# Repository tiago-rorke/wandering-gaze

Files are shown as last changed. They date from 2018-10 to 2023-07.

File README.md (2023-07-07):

# Wandering Gaze

Interactive installation by Ana Teresa Vicente.  
https://anateresavicente.com/wandering-gaze  

The system comprises:
 - core X-Y 2 axisgantry housed in a slightly oversized picture frame
 - a special viewfinder
 	- IR reflectance sensor to detect the person looking through the viewfinder
 	- IR illumination behind a diffusor in the right eye-cup
 	- 45 degree pane of glass reflects the eye into a ps3eye webcam
 	- small LED attached to the side of the webcam lens
 - a tripod containing a mini pc

This installation was largely made possible thanks to the wonderful [EyeWriter](http://eyewriter.org/) project!  We faced a considerable challenge however, in getting (very roughly) accurate tracking from random people approaching the viewfinder without putting them through the calibration process.  We reached a compromise by creating a kind of auto-calibration where a small red dot would appear in the viewers vision when they approach the viewfinder.  They are told to stare at the dot until it disappears, before proceeding to look at the image.  This position is then used to apply an offset to the resulting tracking data to roughly correct it relative to the position of the viewers eye.

## Sources

The eye-tracking sofware is built using the EyeWriter tool and openFrameworks.  
http://eyewriter.org/

CAD model of installation made with Onshape:  
https://cad.onshape.com/documents/b327fc03410528552058d868/w/0ee9eb11091f6ccb3df238ed/e/d6edd997d3fa7512d0595dc8  
the X-Y gantry is based on a previous plotter design:  
https://cad.onshape.com/documents/9c853be8b394a81c5aa6c314/w/0828b5069770ad60c812175c/e/8f06230b793865605afa23f3  
the motion uses the coreXY design:  
http://corexy.org/  
and the structure uses openbuilds:  
https://openbuilds.com/  

The X-Y motion control is done with GRBL  
https://github.com/gnea/grbl  

Arduino is used in the viewfinder and the plotter:  
https://www.arduino.cc/

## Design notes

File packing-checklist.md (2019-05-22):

# Packing Checklist

- Tripod 
    - base
    - 3 metal legs
    - shelf 
    - viewfinder + calibration frame
- Photo frame machine
    - black frame cover 
    - slotted standards
- 1 Ikea stool 
- Screws box 
    - screws
    - power supply + cable
    - viewfinder glass
- Metal shavings box and instructions label
- Debugging box
    ◦ double adapter eu plug
    ◦ router
    ◦ 12v ac-dc adapter + cable
    ◦ 5v ac-dc adapter
    ◦ 2x network patch cables
    ◦ 2x USB micro cables
    ◦ 1x USB mini cable
- Envelope
    - installation assembly and usage overview
    - stool assembly instructions
    - contacts

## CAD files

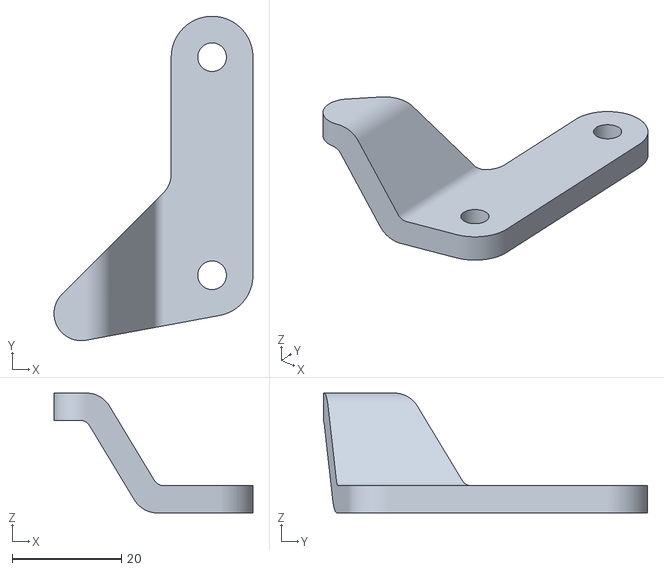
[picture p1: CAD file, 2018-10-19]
design_files/3d_printing/plotter/endstop_batent_v3.stl
36.5 x 59.5 x 22.0

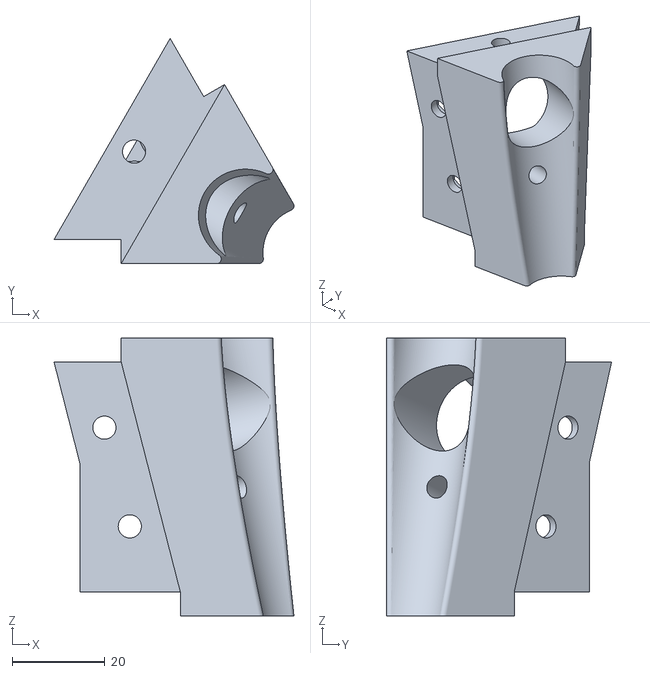
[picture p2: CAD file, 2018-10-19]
design_files/3d_printing/tripe/tripé - corner_right.stl
51.8 x 48.6 x 60.0

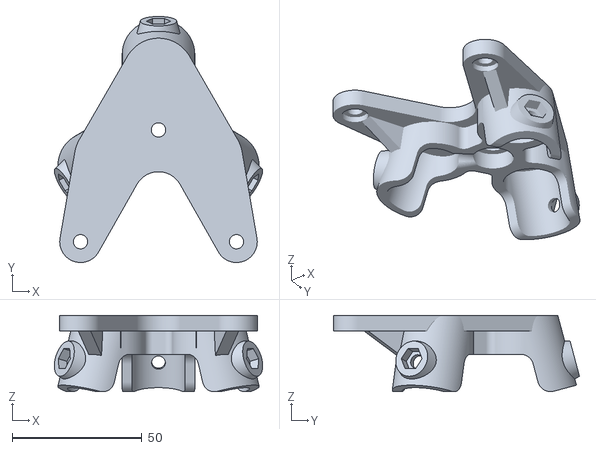
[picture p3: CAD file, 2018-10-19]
design_files/3d_printing/viewfinder/viewfinder v2 - tripod_mount.stl
80.1 x 94.6 x 29.4

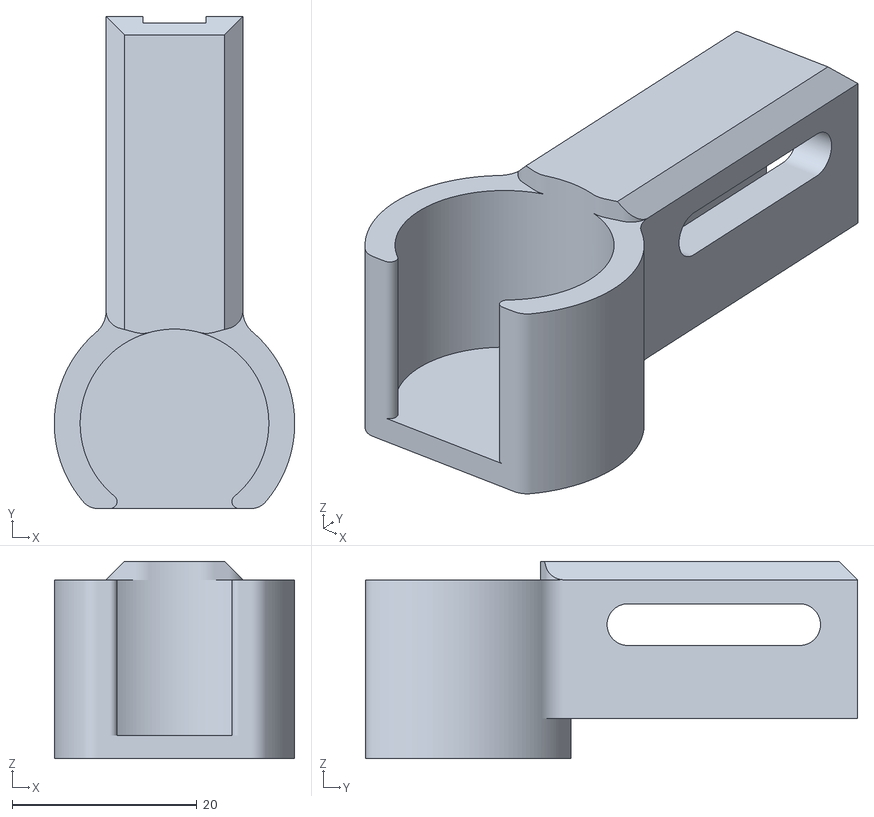
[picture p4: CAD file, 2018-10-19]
design_files/3d_printing/plotter/magnet-holder-20mm_v1.stl
26.0 x 53.2 x 21.4

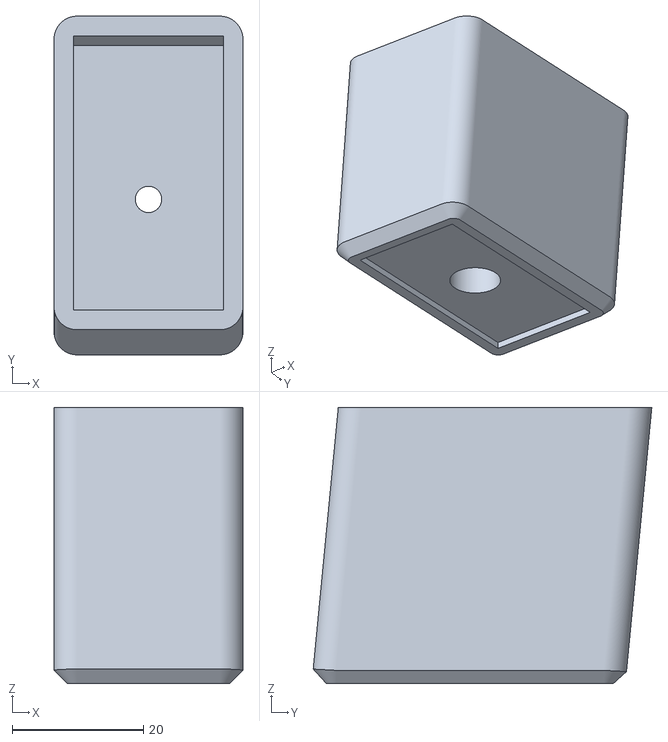
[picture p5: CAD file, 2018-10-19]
design_files/3d_printing/tripe/banco_feet - tall_v2.stl
28.8 x 51.5 x 42.0

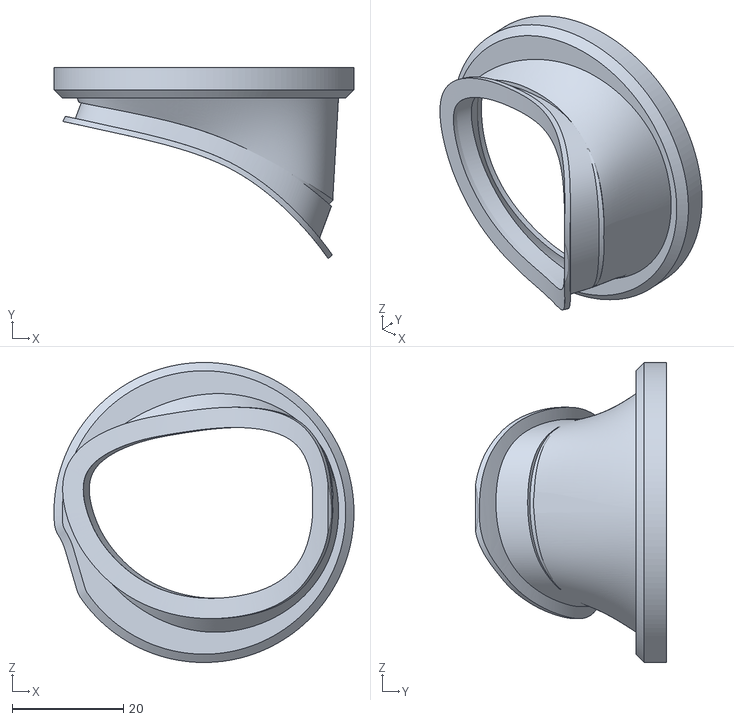
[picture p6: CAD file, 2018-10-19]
design_files/3d_printing/viewfinder/viewfinder v2 - eyecup_right.stl
54.0 x 34.4 x 54.0

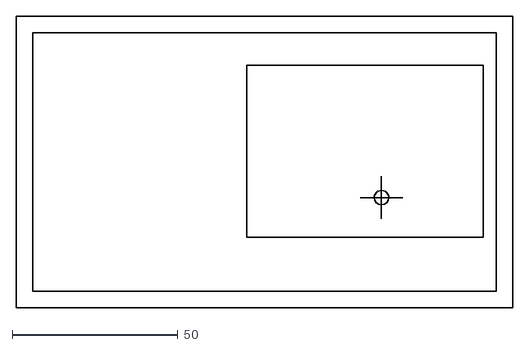
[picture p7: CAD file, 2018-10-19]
design_files/laser_cutting/overlay.dxf
150.0 x 88.0

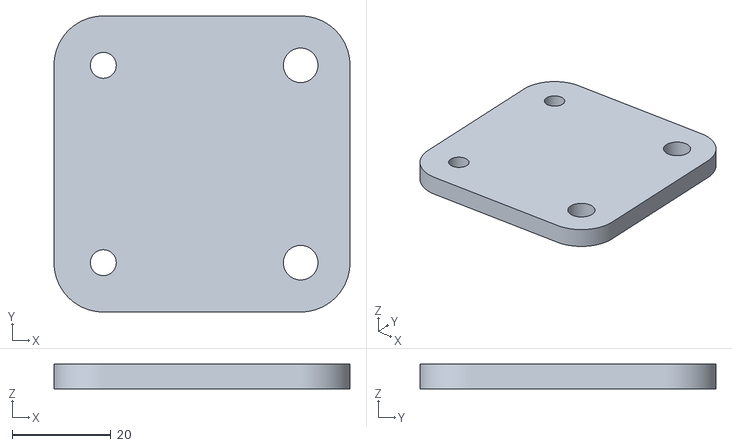
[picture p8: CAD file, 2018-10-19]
design_files/3d_printing/plotter/y-slider-bottom_v1.stl
60.0 x 60.0 x 5.00

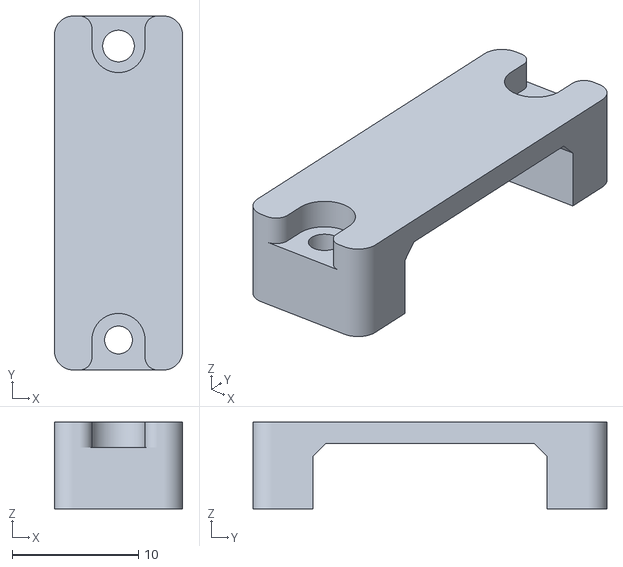
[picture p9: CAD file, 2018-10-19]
design_files/3d_printing/viewfinder/arduino_clip.stl
10.1 x 28.0 x 6.85

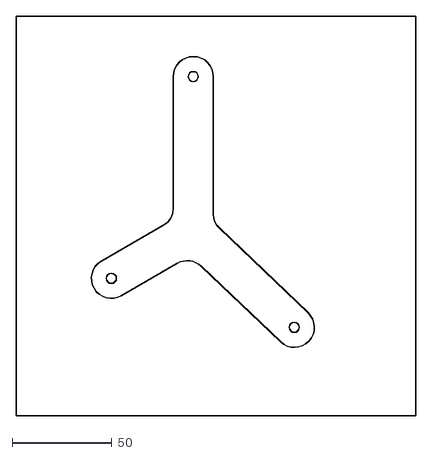
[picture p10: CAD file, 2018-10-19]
design_files/laser_cutting/pc_bracket.dxf
200.0 x 200.0

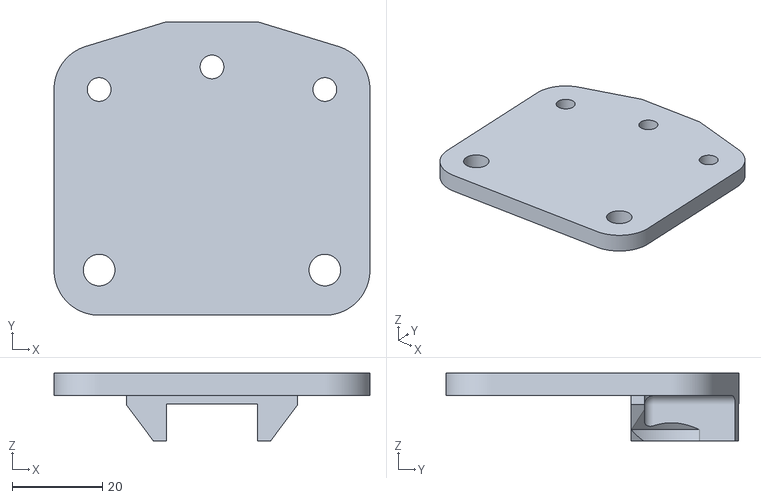
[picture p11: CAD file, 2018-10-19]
design_files/3d_printing/plotter/slider-x-plate_v1.stl
70.0 x 65.0 x 15.0

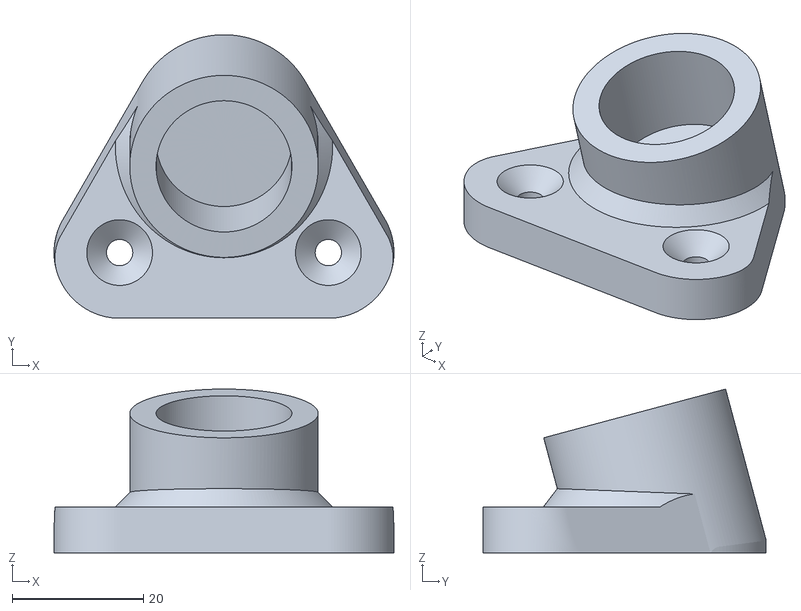
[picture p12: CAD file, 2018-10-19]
design_files/3d_printing/tripe/tripé - foot.stl
51.8 x 43.2 x 25.0

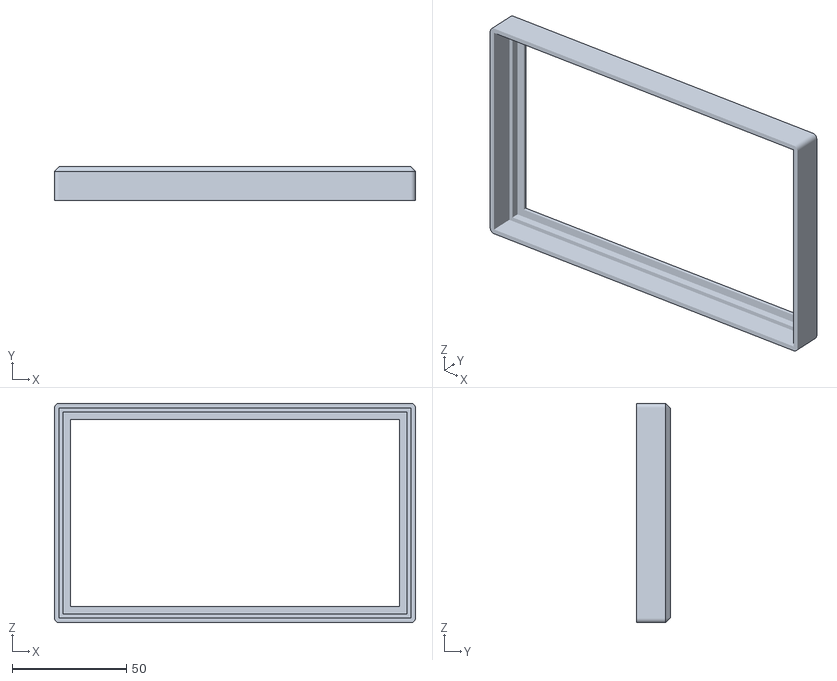
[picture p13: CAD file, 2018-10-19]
design_files/3d_printing/viewfinder/viewfinder v2 - overlay_frame.stl
158.0 x 14.7 x 96.0

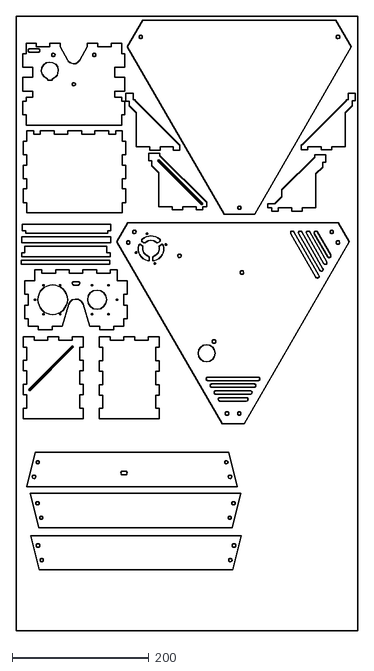
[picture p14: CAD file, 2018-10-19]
design_files/laser_cutting/final_cuts.dxf
500.0 x 900.0

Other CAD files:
design_files/3d_printing/tripe/tripé - corner_left.stl
design_files/3d_printing/plotter/motor-b-bracket_v1.stl
design_files/3d_printing/tripe/banco_feet - short_v2.stl
design_files/3d_printing/viewfinder/viewfinder v2 - eyecup_left.stl
design_files/3d_printing/plotter/glass-brackets_horizontal-v1.stl
design_files/3d_printing/plotter/glass-brackets_lateral-v1.stl
design_files/3d_printing/plotter/idler-a-bracket_v1.stl
design_files/3d_printing/plotter/idler-b-bracket_v1.stl
design_files/3d_printing/plotter/motor-a-bracket_v1.stl
design_files/3d_printing/plotter/y-slider-top_v1.stl
design_files/3d_printing/tripe/tripé - corner_front.stl
design_files/3d_printing/viewfinder/viewfinder v2 - LED_cover.stl
design_files/3d_printing/viewfinder/viewfinder v2 - cam_mount_ball.stl
design_files/3d_printing/viewfinder/viewfinder v2 - cam_mount_socket.stl
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

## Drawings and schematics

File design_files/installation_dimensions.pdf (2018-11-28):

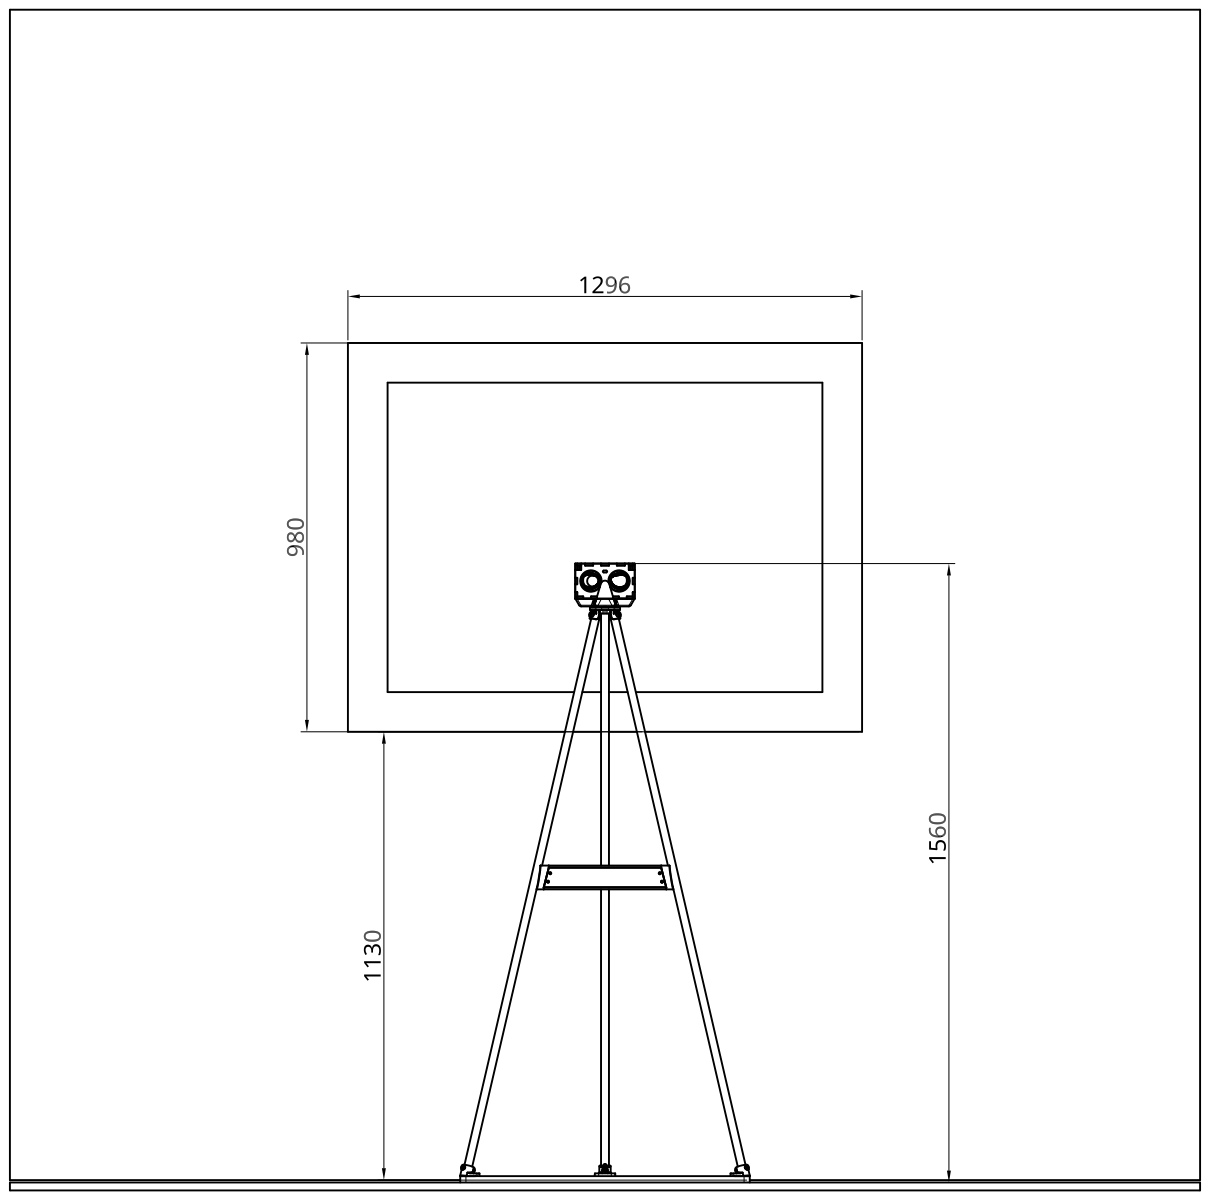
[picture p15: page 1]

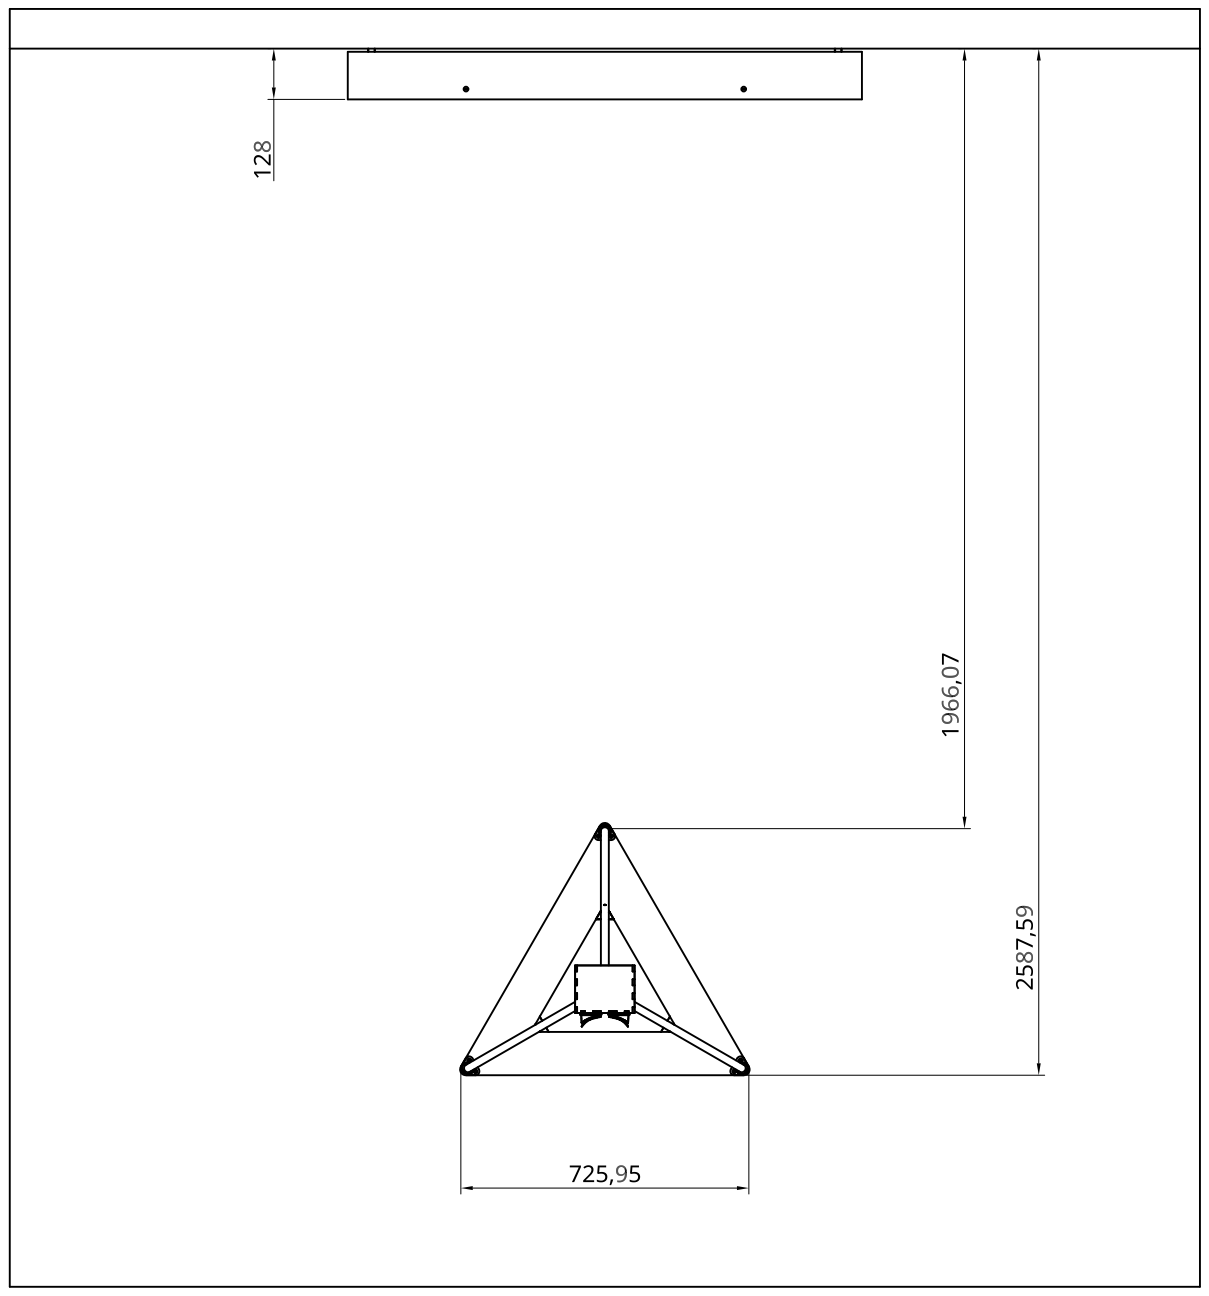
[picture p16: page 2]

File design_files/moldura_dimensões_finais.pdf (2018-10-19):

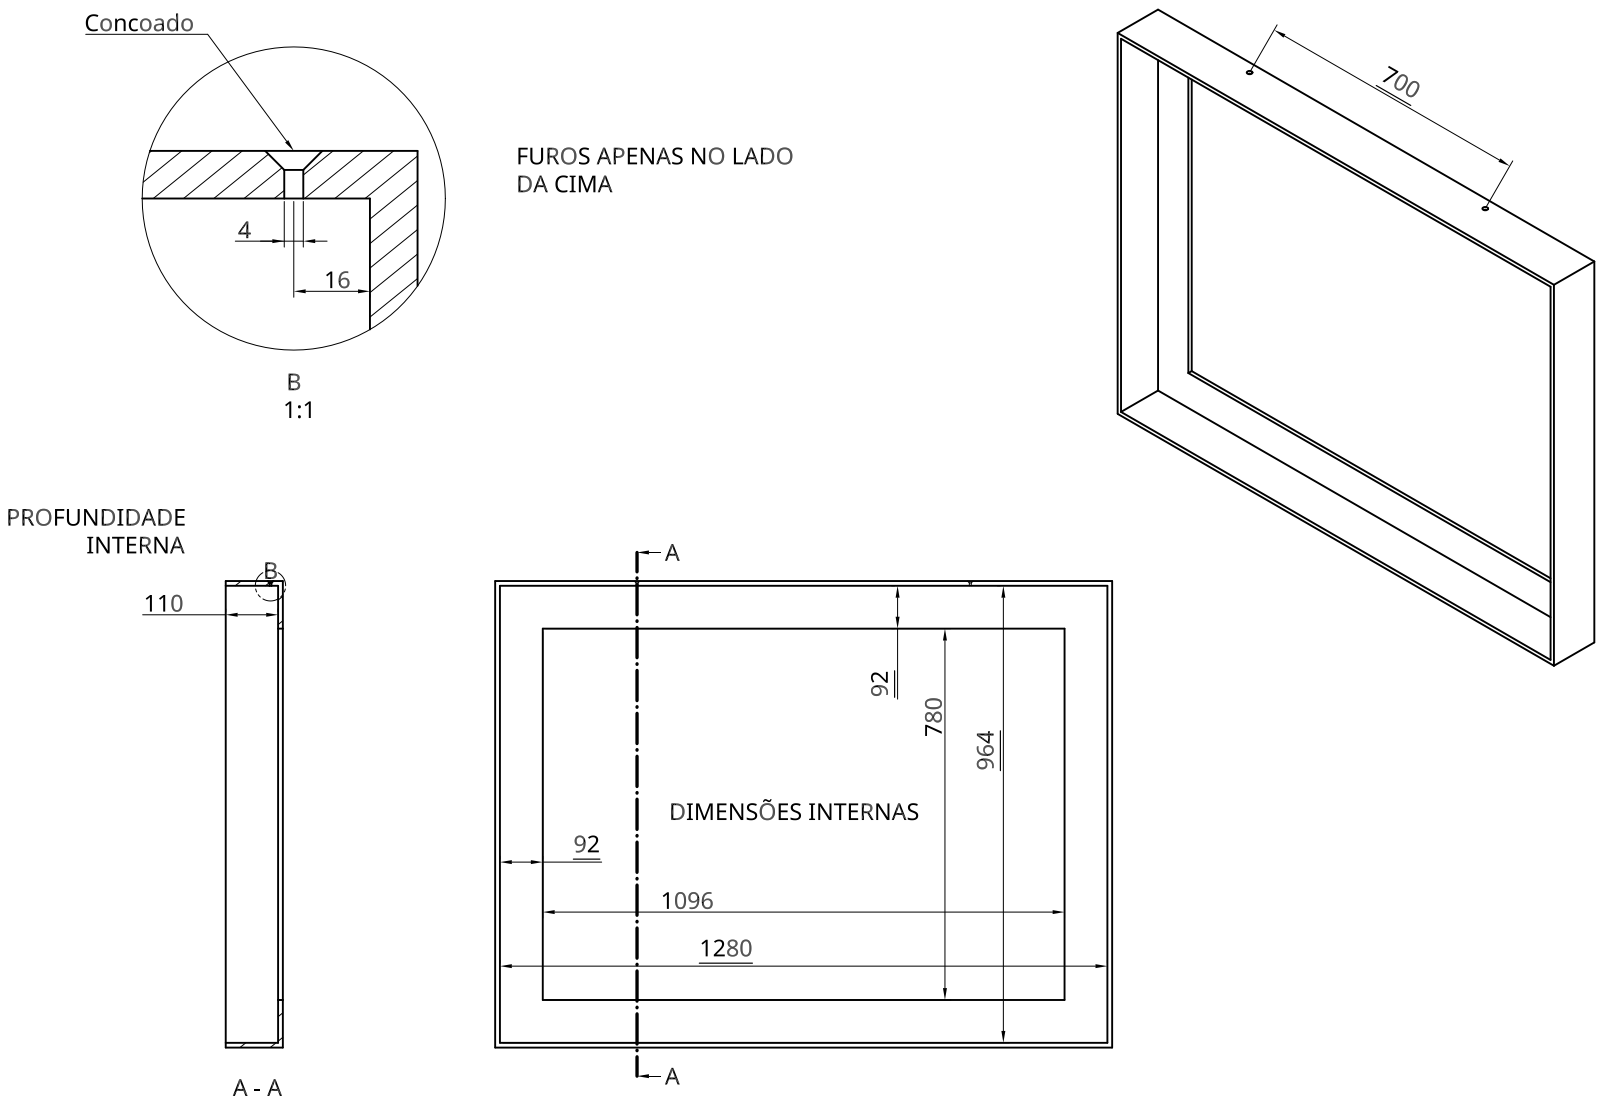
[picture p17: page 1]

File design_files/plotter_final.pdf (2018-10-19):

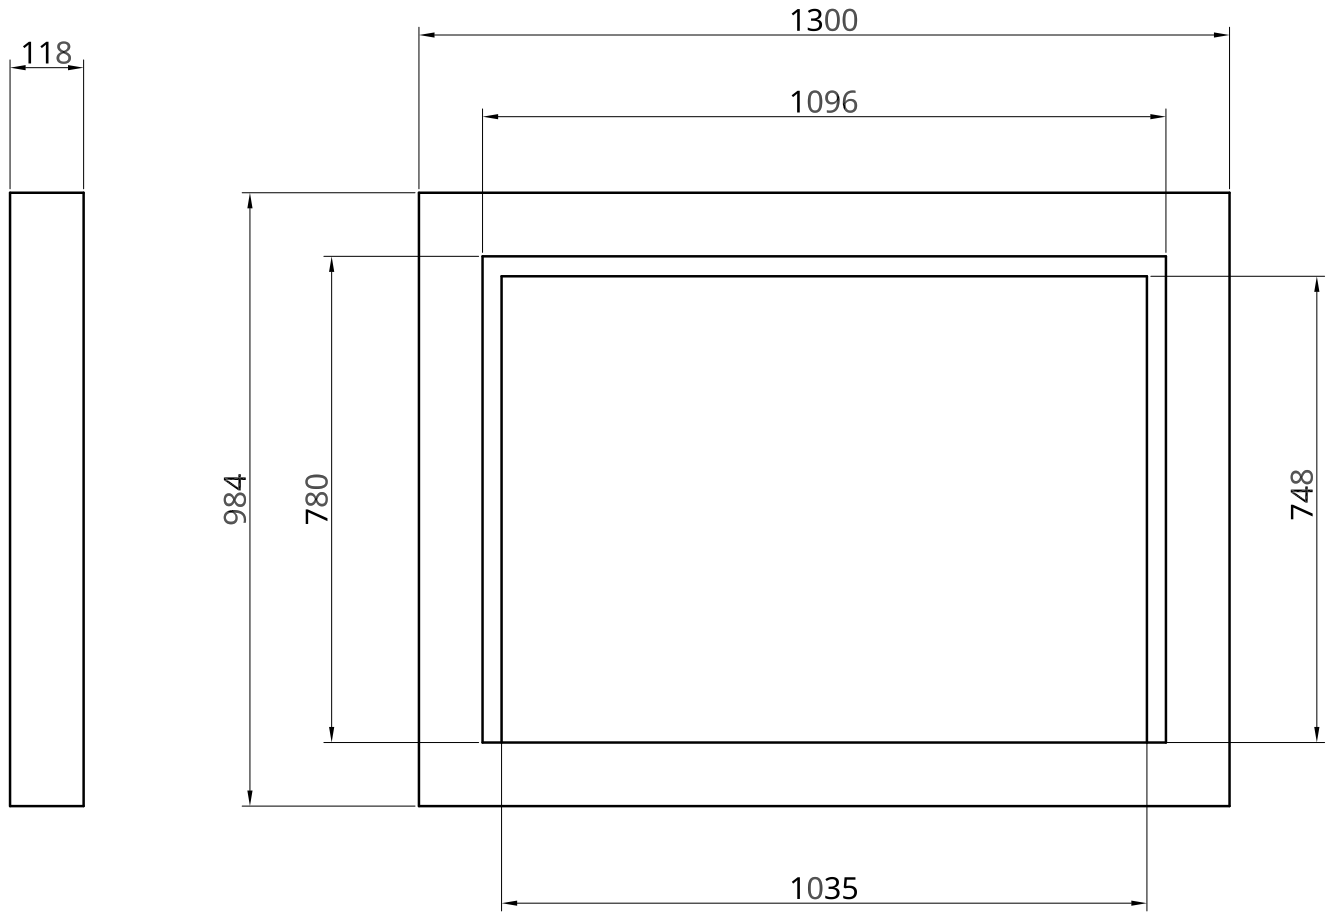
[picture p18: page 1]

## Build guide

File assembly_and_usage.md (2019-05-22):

# Assembly

## Unpacking
1. Remove all the elements from inside the machine, marking them off the checklist.
2. Remove the machine from inside the black frame cover. Lift it out by holding onto the vertical part (the short side) of the aluminium frame, near the black brackets.  **Please do not lift from the horizontal part of the frame, or any other part of the machine.** After removing it, lay the machine face down on the large foam sheet.
3. To remove the black frame cover, first remove some of the surrounding foam.

## Frame  
1. Lift the machine from it's wooden frame, and flip it over so that it is resting on its brackets on the floor.  Slide off the glass cover, and distribute the metal shwarf around the bottom edge of the photo.
2. Clean the glass if necessary and slide it back into the frame.
3. Fix the slotted standards to the wall, taking note of the ends labelled 'top'. The ideal distance to the floor from the bottom edge is 1200mm, the distance between the standards should be 1160mm.
4. Still with the black cover removed, lift the machine again from it's wooden frame, and hang it on the standards. The lower bracket should enter just below the red tape marks.
5. Ensure that the power and usb cables are falling from the center of the frame, and put on the black frame cover.
  
## Tripod  
1. Assemble the three legs to the tripod base, ensuring the power and usb extension cables exit at the front corner of the base, and that the two short usb cables exit at the top of the left leg. Use 3 of the medium length socket-head cap screws.
2.	Remove the top cover of the shelf by unscrewing the three black screws and attach it to the three legs, taking note of the front label and passing the cables through the holes in the corners. Use 3 of the long cap screws.
3. Connect all the cables in the box following the labels, and also the unique fan connector which is not labelled. Fasten the lid of the box using the 3 short low profile cap screws.

## Viewfinder  
1. Attach the viewfinder mount to the base of the tripod using the remaining 3 long cap screws, first putting the springs in holes with the larger spring in the center hole. Take turns tightening each screw until the viewfinder is level and there is about a 5mm gap between the base of the viewfinder and the mount.
2. Sit the viewfinder on the top of the tripod ensuring it is facing forwards. Fasten using the 3 short cap screws.
3. Connect the two usb cables to the corresponding sockets on the viewfinder.  
4. If necessary, clean the glass pane, then insert it into the slot of the viewfinder.  

# Powering On/Off
- The power button of the PC can be accessed via a hole on the bottom of the box.  Press the button once to power on or to power off.  It is not necessary to hold down the button.  While powering on or off, the light visible from the front of the box will be green.  When the system has finished booting it will be blue.  When powering off, please wait for the green light to turn off before unplugging or switching off the power.
- While the eyetracking program is starting up, the red led in the viewfinder will be blinking. Once it is ready to use the led will be off.

# Calibration  
Before the installation can be used the position of the viewfinder must be carefully adjusted:  
1. Make sure the system is powered on and ready to use and put the calibration frame on the viewfinder, with the right eye looking through the grid.
2. Adjust the 3 screws holding the viewfinder, moving the tripod if necessary, until both:  
	- the edges of the inside of the frame are aligned with the boundaries of the grid on the overlay.  
	- and the red led of the viewfinder is aligned with the center of the cross of the grid.  
3. Once adjusted, remove the calibration frame.

# Usage
- When someone looks through the viewfinder, they will see a red light appear.  They must look at the light until it disappears, at which point they can look at the photograph.
- Once they step away from the viewfinder, the machine will begin to retrace the path the viewer's eye has taken, spending more time in the areas where the viewer's gaze has lingered.

# Troubleshooting
- If the red light doesn't come on, or is on and doesn't turn off, please shut down the system, unplug the usb cables from the viewfinder, wait a few seconds, plug them back in and turn it back on again.
- If the red light is blinking, or doesn't stop blinking after powering on the PC, please unplug the usb cable from the viewfinder (the one closest to front/eyepiece side of the viewfinder), wait a few seconds, and plug it back in.  If it is still blinking after 15s or so, do the same with the usb connection to the machine.  If it is still blinking, try powering the PC off and on again.

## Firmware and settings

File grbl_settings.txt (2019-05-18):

$0=10
$1=25
$2=0
$3=3
$4=0
$5=0
$6=0
$10=0
$11=0.010
$12=0.002
$13=0
$20=1
$21=1
$22=1
$23=3
$24=500.000
$25=20000.000
$26=250
$27=1.000
$30=1000
$31=0
$32=0
$100=80.000
$101=80.000
$102=250.000
$110=10000.000
$111=10000.000
$112=500.000
$120=500.000
$121=500.000
$122=10.000
$130=1036.000
$131=751.000
$132=200.000

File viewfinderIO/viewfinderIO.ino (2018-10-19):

#define LED 3
#define EYE_LEDS_1 5
#define EYE_LEDS_2 6
#define EYE_LEDS_3 9
#define FACE_SENSOR A5
#define FACE_SENSOR_POWER A4
#define LED_DEFAULT 100

String inString = "";

int ledLevel = LED_DEFAULT;
int faceState = 0;
int eyeLedLevel = 0;
int faceThreshold = 800;

int serialInterval = 100;
long serialTimer = 0;

int blinkInterval = 500; // LED blinks while serial is not connected
long blinkTimer = 0;

boolean connected = false;
int connectionTimeout = 5000; // if nothing is received over serial after a while, change state to disconnected.
long connectionTimer;

void setup() {
		
	pinMode(LED, OUTPUT);
	pinMode(EYE_LEDS_1, OUTPUT);
	pinMode(EYE_LEDS_2, OUTPUT);
	pinMode(EYE_LEDS_3, OUTPUT);
	pinMode(FACE_SENSOR, INPUT);
	pinMode(FACE_SENSOR_POWER, OUTPUT);

	serialTimer = millis();
	blinkTimer = millis();
	connectionTimer = millis();

	analogWrite(LED, ledLevel);
	digitalWrite(FACE_SENSOR_POWER, LOW);

	Serial.begin(115200);

	Serial.println("ready");
}


void loop() {

	analogWrite(LED, ledLevel);
	analogWrite(EYE_LEDS_1, 255 - eyeLedLevel);
	analogWrite(EYE_LEDS_2, 255 - eyeLedLevel);
	analogWrite(EYE_LEDS_3, 255 - eyeLedLevel);

	if(connected && millis() - connectionTimer > connectionTimeout) {
		connected = false;
		ledLevel = 0;
		digitalWrite(FACE_SENSOR_POWER, LOW);
	}

	if(!connected && millis() - blinkTimer > blinkInterval) {
	
		ledLevel = abs(ledLevel - LED_DEFAULT); // switches between 0 and LED_DEFAULT.
		blinkTimer = millis();
	
	} else if(connected && millis() - serialTimer > serialInterval) {
		faceState = analogRead(FACE_SENSOR);
		if(faceState < faceThreshold) {
			Serial.println(1);
		} else {
			Serial.println(0);			
		}
		serialTimer = millis();
	}

	while(Serial.available() > 0) {
		char inChar = Serial.read();
		if(inChar == '\n') {
			parseVars(inString);
		} else {
			inString += inChar;
		}
		//connected = true;
		//digitalWrite(FACE_SENSOR_POWER, HIGH);
		connectionTimer = millis();
	}

}


void parseVars(String s) {  

	char cmd = s.charAt(0);
	String varString = s.substring(1, s.length());
	int var = varString.toInt();

	switch(cmd) {

		case 'L':
			ledLevel = var;
			break;

		case 'E':
			eyeLedLevel = var;
			break;

		case 'T':
			faceThreshold = var;
			break;
	}

	switch(cmd) {		
		case 'L':
		case 'E':
		case 'T':
			if(!connected) ledLevel = 0;
			connected = true;
			digitalWrite(FACE_SENSOR_POWER, HIGH);
			break;
	}

	/*
	Serial.print(cmd);
	Serial.print(" = ");
	Serial.println(var);
	*/
	inString = "";

}

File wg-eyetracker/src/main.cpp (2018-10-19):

#include "ofMain.h"
#include "wg-eyetracking.h"


//========================================================================
int main( ){

   ofAppGLFWWindow window;
	ofSetupOpenGL(&window, 1920,1080, OF_FULLSCREEN);			// <-------- setup the GL context

	// this kicks off the running of my app
	// can be OF_WINDOW or OF_FULLSCREEN
	// pass in width and height too:
	ofRunApp( new eyetracking());

}

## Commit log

2018-10-19 committing all the things
    [arduino_clip.stl, banco_feet - short_v2.stl, banco_feet - tall_v2.stl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]
2019-05-18 add grbl settings
    [grbl_settings.txt]
2019-05-21 remove duplicate grbl ssettingssettings file
2019-05-22 fix assembly instructions
2019-09-04 adjust viewfinder face detect sensor threshold
